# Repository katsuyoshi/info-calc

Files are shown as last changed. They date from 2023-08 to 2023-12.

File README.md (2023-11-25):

# 情報電卓 (Info Calc)

## 概要

電卓を様々な情報を表示する表示器にします。  
ESP NOWで外部からデータを受信することで温度や湿度など様々なデータを表示できます。  
[タイマー表示させるサンプル](platformio/timer_publisher)をM5StickCに書き込むみAボタンをおしてタイマーをスタートさせるとタイマー表示が確認できます。

protopediaに登録していますので、そちらもご覧ください。

[情報電卓](https://protopedia.net/prototype/4227)

## 材料

- 電卓 Canon WS-1200H (恐らく廃品)
- M5Atom Matrix x 1
- FS90 x 3

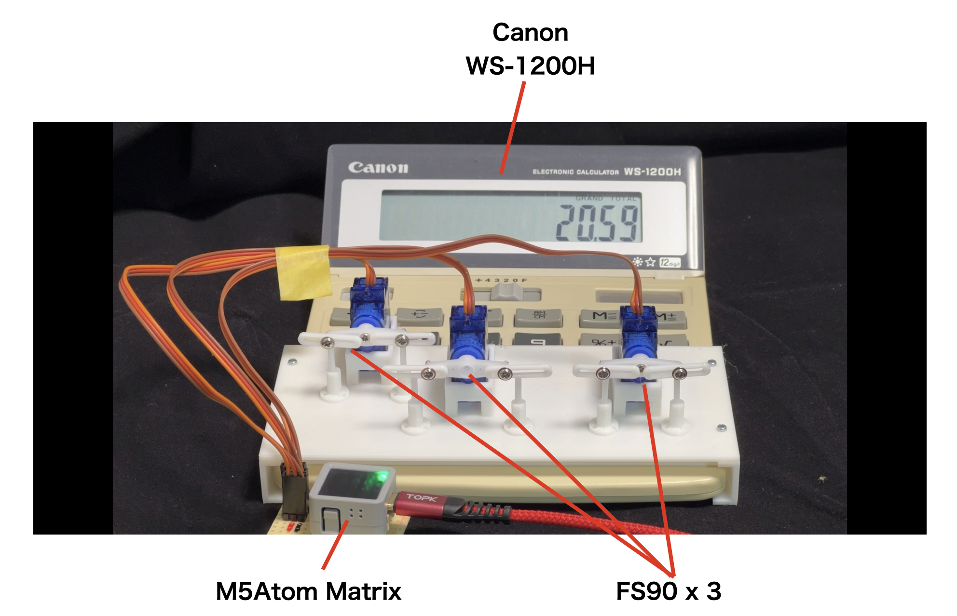
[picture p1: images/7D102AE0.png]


## 作り方

### 部品印刷

以下の2つの3Dモデルデータを3Dプリンターで印刷します。  
電卓によって変わるので設計し直しが必要と思われます。(データは参考程度です。)  

- [base_and_pushers.gcode](/3dmodels/base_and_pushers.gcode)
- [spacer.gcode](/3dmodels/spacer.gcode)

M2x6mmのネジでサイドの押さえと上面を止めます。  
サーボモーターもM2x6mmで止めます。  

棒状のサーボホーンとプッシャーをサーボモーター付属のネジで止めます。  

### 配線

以下の組みあせで配線します。

|M5Atom Matrix|FS90(=,+用)|FS90(.,0用)|FS90(1,CA用)|FS90(,-用)|備考|
|:--|:--|:--|:--|:--|:--|
|G22|橙||||100Ωの抵抗を間に入れてます|
|G19||橙|||100Ωの抵抗を間に入れてます|
|G23|||橙||100Ωの抵抗を間に入れてます|
|G33||||橙|100Ωの抵抗を間に入れてます|
|5V|赤|赤|赤|赤||
|GND|茶|茶|茶|茶||

### ソフトウェア書き込み

- このリポジトリをダウンロードします。
- VSCodeにPlatformIO拡張モジュールインストールし、[platformio/info_calc](/platformio/info_calc)フォルダを開きます。  
- 必要なライブラリーなど自動で読み込まれますので終わるまで待ちます。(下部ステータスバーでローディングのアニメーションが見えてる間)
- env.h.sampleをコピーしenv.hを作成します。
- 定数定義にSSIDとパスワードを書き込みます。
- USBケーブルでPCとM5Atom Matrixを繋ぎます。
- 下部ステータスバーの書き込みアイコン(レ点)を押して書き込みます。

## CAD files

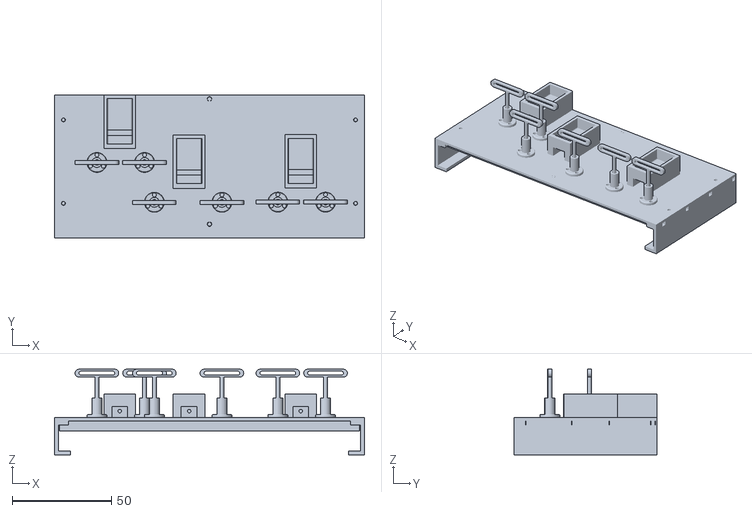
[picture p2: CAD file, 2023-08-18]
3dmodels/assembly.stl
156.0 x 72.1 x 43.1

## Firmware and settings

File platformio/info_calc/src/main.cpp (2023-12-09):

/*
MIT License

Copyright (c) 2023 Katsuyoshi Ito

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
THE SOFTWARE IS PROVIDED "AS IS", WITHOUT WARRANTY OF ANY KIND, EXPRESS OR
IMPLIED, INCLUDING BUT NOT LIMITED TO THE WARRANTIES OF MERCHANTABILITY,
FITNESS FOR A PARTICULAR PURPOSE AND NONINFRINGEMENT. IN NO EVENT SHALL THE
AUTHORS OR COPYRIGHT HOLDERS BE LIABLE FOR ANY CLAIM, DAMAGES OR OTHER
LIABILITY, WHETHER IN AN ACTION OF CONTRACT, TORT OR OTHERWISE, ARISING FROM,
OUT OF OR IN CONNECTION WITH THE SOFTWARE OR THE USE OR OTHER DEALINGS IN THE
SOFTWARE.
 */

#include <Arduino.h>
#include <M5Unified.h>
#include <ESP32Servo.h>
#include <WiFi.h>
#include <FastLED.h>
#include <time.h>
#include <esp_now.h>
#include "led.h"
#include "pusher.h"
#include "light.h"
#include "env.h"

// for LEDs
#define NUM_LEDS 25
#define LED_DATA_PIN 27
#define BRIGHTNESS  50

CRGB leds[NUM_LEDS];

// for ntp server

static const char *ntpServer = "ntp.nict.jp";
static const long gmtOffset_sec = 9 * 3600;
static const int daylightOffset_sec = 0;

static bool time_available = false;
static struct tm currentTime;


#define INVALID_DATA_INTERVAL   1 * 60 * 60 * 1000

// showing data rounding
#define ROUNDING_INTERVAL      30 * 1000

static bool rounding = false;
static unsigned long rounding_at = 0;

// Light pattern
enum LightPattern {
    LIGHT_OFF,
    LIGHT_NORMAL,
    LIGHT_JUST_HOUR,
    LIGHT_TIMER,
    LIGHT_LESS_ONE_MINITUE,
    LIGHT_LESS_THIRTY_SECONDS,
    LIGHT_LESS_TEN_SECONDS,
    LIGHT_LESS_FIVE_SECONDS,
    LIGHT_BANG,
    LIGHT_THREE_FEAVER,
    LIGHT_FOUR_FEVER,
};


struct ChannelValue {
    float value;
    unsigned long received_at;
    bool available;
    char unit[16];
};

static Pusher pushers[] = {
    Pusher(22, 11, 10, 9),      // A: =, B: +
    Pusher(19, 16, 17, 9),      // A: ., B: 0
    Pusher(23, 16, 16, 11),     // A: 1, B: CA
    Pusher(33, 10, 10, 8),      // A:  , B: -
};

static Light light = Light(32, 26, 25);

void move_servos()
{
    for (int i = 0; i < 3; i++)
    {
        pushers[i].move_next();
    }
}

// display time on a calculator.
class Calculator
{
    typedef enum
    {
        Unknown,
        Clear,

        Add1Minute,
        Add10Minutes,

        Add1Hour,
        Add10Hours,
        Add100Hours,

        Sub1Minute,
        Sub10Minutes,

        Sub1Hour,
        Sub10Hours,
        Sub100Hours,
    } mode;

    typedef enum
    {
        UnitUnknown,
        UnitClock,
        UnitTimer,
        UnitTemperature,
        UnitHumidity,
    } unit_type;

private:
    mode _mode = Unknown;
    int _value = 0;
    int _digit_values[4];
    char *_unit_pattern;
    unit_type _unit = UnitClock;
    LightPattern _light_pattern = LIGHT_NORMAL;

public:

    unit_type unit() { return _unit; }
    LightPattern light_pattern() { return _light_pattern; }
    void set_light_pattern(LightPattern pat) { _light_pattern = pat; }

    void set_time(int hour, int minute)
    {
        if (_mode == Unknown)
        {
            clear_all();
        }
        set_unit("clock");
        set_value((float)hour + (float)minute / 100.0);
    }

    void set_channel_value(ChannelValue *channel_value) {
        if (channel_value->available == false) { return; }

        set_unit(channel_value->unit);
        set_value(channel_value->value);
    }

    void clear_all()
    {
        push_clear_all();
        push_equal();
        _mode = Clear;
        _value = 0;
        for (int i = 0; i < 4; i++) {
            _digit_values[i] = 0;
        }
        _unit_pattern = NULL;
    }

    void set_unit(const char *unit) {
        const char *units[] = {
            "clock",
            "timer",
            "°C",
            "%"
        };

        int num = sizeof(units) / sizeof(units[0]);
        const char **ptr = &units[0];
        char *pattern = NULL;

        for (int i = 0; i < num; i++) {
            if (strcmp(*ptr++, unit) == 0) {
                switch (i) {
                    case 0:
                        pattern = led_clock_pattern;
                        _unit = UnitClock;
                        break;
                    case 1:
                        pattern = led_timer_pattern;
                        _unit = UnitTimer;
                        break;
                    case 2:
                        if (_value < 1000) {
                            pattern = led_cold_temperature;
                        } else
                        if (_value > 2500) {
                            pattern = led_hot_temperature;
                        } else {
                            pattern = led_norm_temperature;
                        }
                        _unit = UnitTemperature;
                        break;
                    case 3:
                        if (_value < 3333) {
                            pattern = led_low_humidity;
                        } else
                        if (_value > 6666) {
                            pattern = led_high_humidity;
                        } else {
                            pattern = led_norm_humidity;
                        }
                        _unit = UnitHumidity;
                        break;
                    default:
                        _unit = UnitUnknown;
                        break;
                }
            }
        }

        if (pattern == NULL) { return; }
        if (pattern == _unit_pattern) { return; }
        _unit_pattern = pattern;
        Serial.println(_unit_pattern);

        char *ch = _unit_pattern;
        // Reverse the order of the set values for an upside-down arrangement.
        for (int i = NUM_LEDS - 1; i >= 0; i--) {
            switch (*ch++) {
                case 'R':
                    leds[i] = CRGB::Red;
                    break;
                case 'G':
                    leds[i] = CRGB::Green;
                    break;
                case 'B':
                    leds[i] = CRGB::Blue;
                    break;
                default:
                    leds[i] = CRGB::Black;
                    break;
            }
        }
        FastLED.show();
    }

#if defined(TEST_MODE) || defined(TEST_COUNT_UP_DOWN)
public:
#else
private:
#endif

    void push_clear_all()
    {
        pushers[2].push_b();
        Serial.print("C");
    }

    void push_one()
    {
        pushers[2].push_a();
        Serial.print("1");
    }

    void push_zero()
    {
        pushers[1].push_b();
        Serial.print("0");
    }

    void push_dot()
    {
        pushers[1].push_a();
        Serial.print(".");
    }

    void push_plus()
    {
        pushers[0].push_b();
        Serial.print("+");
    }

    void push_equal()
    {
        pushers[0].push_a();
        Serial.print("=");
    }

    void push_minus()
    {
        pushers[3].push_b();
        Serial.print("-");
    }

private:

    void add_ten_minutes(int times)
    {
        if (times == 0)
        {
            return;
        }
        if (_mode != Add10Minutes)
        {
            push_plus();
            push_dot();
            push_one();
            _mode = Add10Minutes;
        }
        for (int i = 0; i < times; i++)
        {
            push_equal();
            _value += 10;
        }
    }

    void sub_ten_minutes(int times)
    {
        if (times == 0)
        {
            return;
        }
        if (_mode != Sub10Minutes)
        {
            push_minus();
            push_dot();
            push_one();
            _mode = Sub10Minutes;
        }
        for (int i = 0; i < times; i++)
        {
            push_equal();
            _value -= 10;
        }
    }

    void add_one_minute(int times)
    {
        if (times == 0)
        {
            return;
        }
        if (_mode != Add1Minute)
        {
            push_plus();
            push_dot();
            push_zero();
            push_one();
            _mode = Add1Minute;
        }
        for (int i = 0; i < times; i++)
        {
            push_equal();
            _value += 1;
        }
    }

    void sub_one_minute(int times)
    {
        if (times == 0)
        {
            return;
        }
        if (_mode != Sub1Minute)
        {
            push_minus();
            push_dot();
            push_zero();
            push_one();
            _mode = Sub1Minute;
        }
        for (int i = 0; i < times; i++)
        {
            push_equal();
            _value -= 1;
        }
    }

    void add_hundred_hours(int times)
    {
        if (times == 0)
        {
            return;
        }
        if (_mode != Add100Hours)
        {
            push_plus();
            push_one();
            push_zero();
            push_zero();
            _mode = Add100Hours;
        }
        for (int i = 0; i < times; i++)
        {
            push_equal();
            _value += 10000;
        }
    }

    void sub_hundred_hours(int times)
    {
        if (times == 0)
        {
            return;
        }
        if (_mode != Sub100Hours)
        {
            push_minus();
            push_one();
            push_zero();
            push_zero();
            _mode = Sub100Hours;
        }
        for (int i = 0; i < times; i++)
        {
            push_equal();
            _value -= 10000;
        }
    }

    void add_ten_hours(int times)
    {
        if (times == 0)
        {
            return;
        }
        if (_mode != Add10Hours)
        {
            push_plus();
            push_one();
            push_zero();
            _mode = Add10Hours;
        }
        for (int i = 0; i < times; i++)
        {
            push_equal();
            _value += 1000;
        }
    }

    void sub_ten_hours(int times)
    {
        if (times == 0)
        {
            return;
        }
        if (_mode != Sub10Hours)
        {
            push_minus();
            push_one();
            push_zero();
            _mode = Sub10Hours;
        }
        for (int i = 0; i < times; i++)
        {
            push_equal();
            _value -= 1000;
        }
    }

    void add_one_hour(int times)
    {
        if (times == 0)
        {
            return;
        }
        if (_mode != Add1Hour)
        {
            push_plus();
            push_one();
            _mode = Add1Hour;
        }
        for (int i = 0; i < times; i++)
        {
            push_equal();
            _value += 100;
        }
    }

    void sub_one_hour(int times)
    {
        if (times == 0)
        {
            return;
        }
        if (_mode != Sub1Hour)
        {
            push_minus();
            push_one();
            _mode = Sub1Hour;
        }
        for (int i = 0; i < times; i++)
        {
            push_equal();
            _value -= 100;
        }
   }

    void set_digit(int number, int digit) {
        if (number == 0) { return; }

        bool sign = number >= 0;
        number = abs(number);
        if (number > 5) {
            number = 10 - number;
            sign = !sign;
        }

        switch (digit) {
            case 0:
                {
                    if (sign) {
                        add_one_minute(number);
                    } else {
                        sub_one_minute(number);
                    }
                }
                break;
            case 1:
                {
                    if (sign) {
                        add_ten_minutes(number);
                    } else {
                        sub_ten_minutes(number);
                   }
                }
                break;

            case 2:
                {
                    if (sign) {
                        add_one_hour(number);
                    } else {
                        sub_one_hour(number);
                    }
                }
                break;
            case 3:
                {
                    if (sign) {
                        add_ten_hours(number);
                    } else {
                        sub_ten_hours(number);
                    }
                }
                break;
            case 4:
                {
                    if (sign) {
                        add_hundred_hours(number);
                    } else {
                        sub_hundred_hours(number);
                    }
                }
                break;
            defualt:
                return;
        }
    }

#if defined(TEST_MODE) || defined(TEST_COUNT_UP_DOWN)
public:
#endif

    void set_value(float value) {
        int v = (value * 100 + 0.5);
        if (_value == v) return;

Serial.printf("set_value %.2f -> \t", value);

        int base = 1;

        for (int digit = 0; digit < 5; digit++) {
            if (_value == v) break;
            int n = v - _value;
            n = (n / base) % 10;
            set_digit(n, digit);
            base *= 10;
        }
Serial.printf("\t-> _value %d, v: %d\n", _value, v);

Serial.printf("unit %d\n", _unit);
        switch(_unit) {
        case UnitTimer:
            if (_value >= 100) {
                _light_pattern = LIGHT_TIMER;
            } else
            if (_value >= 30) {
                _light_pattern = LIGHT_LESS_ONE_MINITUE;
            } else
            if (_value >= 10) {
                _light_pattern = LIGHT_LESS_THIRTY_SECONDS;
            } else
            if (_value >= 5) {
                _light_pattern = LIGHT_LESS_TEN_SECONDS;
            } else
            if (_value > 0) {
                _light_pattern = LIGHT_LESS_FIVE_SECONDS;
            } else {
                _light_pattern = LIGHT_FOUR_FEVER;
            }
            break;

        case UnitClock:
            if ((_value % 100 == 0) && (currentTime.tm_sec < 2)) {
                _light_pattern = LIGHT_JUST_HOUR;
                break;
            } else {
                _light_pattern = LIGHT_NORMAL;
                // 分が00でない場合はdefaultでも判断させるためbreakなし。
            }

        default:
            if ((_value < 1000) && (_value % 111 == 0)) {
                _light_pattern = LIGHT_THREE_FEAVER;
            } else
            if (_value % 1111 == 0) {
                _light_pattern = LIGHT_FOUR_FEVER;
            } else {
                _light_pattern = LIGHT_NORMAL;
            }
            break;
        }
    }
};

static Calculator calc = Calculator();

#define NUMBER_OF_CHANNEL       11

static int current_channel = 0;
static struct ChannelValue channel_values[NUMBER_OF_CHANNEL];
static unsigned long last_received_at = 0;

static esp_now_peer_info_t espnow_slave;
static bool espnow_setuped = false;

static void set_rounding(bool f, bool update = false) {
    if (update == false && rounding == f) { return; }
    
    rounding = f;
    if (update) {
        rounding_at = millis();
    } else {
        // for rounding immediately
        rounding_at = millis() - ROUNDING_INTERVAL;
    }
}

static void update_time()
{
    if (!getLocalTime(&currentTime))
    {
        Serial.println("Failed to obtain time");
        return;
    }
    time_available = true;
    Serial.println(&currentTime, "%Y %m %d %a %H:%M:%S");
}

static void espnow_on_data_receive(const uint8_t *mac_addr, const uint8_t *data, int data_len)
{
    ushort ch = 0;
    float value = 0.0f;
    char unit[16] = { 0 };
    char buff[64] = { 0 };
    ChannelValue *channel_value;

    strncpy(buff, (const char *)data, min(data_len, 63));
    
    sscanf(buff, "%hd,%f,%s\n", &ch, &value, unit);
    if (ch < 1 || ch >= NUMBER_OF_CHANNEL) {
        Serial.printf("The channell is %d. ", ch);
        Serial.println("The channel should 1 to 10.");
        return;
    }

    channel_value = &channel_values[ch];
    channel_value->available = true;
    channel_value->value = value;
    channel_value->received_at = millis();
    strncpy(channel_value->unit, unit, 15);

    Serial.printf("<< %s\n", buff);

    // タイマーの場合は継続して表示させるためラウンデングモードにせず直ぐにチャンネルを変更する。
    bool rounding = strcmp(unit, "timer") != 0;
    if (rounding == false) {
        current_channel = ch;
    }
    set_rounding(rounding);
    last_received_at = millis();
}

// @refer: https://it-evo.jp/blog/blog-1397/
static void espnow_setup_if_needed()
{
    if (espnow_setuped) return;

    WiFi.mode(WIFI_STA);
    WiFi.disconnect();
    if (esp_now_init() == ESP_OK)
    {
        Serial.println("ESPNow Init Success");
        espnow_setuped = true;
    }
    else
    {
        Serial.println("ESPNow Init Failed");
        espnow_setuped = false;
        ESP.restart();
        return;
    }

    memset(&espnow_slave, 0, sizeof(espnow_slave));
    for (int i = 0; i < 6; ++i)
    {
        espnow_slave.peer_addr[i] = (uint8_t)0xff;
    }

    esp_err_t addStatus = esp_now_add_peer(&espnow_slave);
    if (addStatus == ESP_OK)
    {
        Serial.println("Pair success");
    }
    esp_now_register_recv_cb(espnow_on_data_receive);
    last_received_at = millis();
}
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
void loop()
{
    static int n = 0;
    static int test_state = 0;
    M5.update();

#ifdef TEST_MODE
    test_mode();
    return;
#endif
#ifdef TEST_COUNT_UP_DOWN
    test_count_up_down();
    return;
#endif
#ifdef TEST_LIGHT_PATTERN
    test_light_patter();
    return;
#endif

    // Set it invalid after one hour past
    unsigned long now = millis();
    bool needs_to_change_current_channel = false;
    for (int i = 1; i < NUMBER_OF_CHANNEL; i++) {
        ChannelValue *channel_value = &channel_values[i];

        if (channel_value->available &&
            (now - channel_value->received_at >= INVALID_DATA_INTERVAL)) {
            channel_value->available = false;
            Serial.println("Invalid data");
            if (i == current_channel) {
                needs_to_change_current_channel = true;
            }
        }
    }

    // ラウンディングモード時はROUNDING_INTERVAL経過で次のチャンネルを表示する。
    if (rounding) {
        if (now - rounding_at >= ROUNDING_INTERVAL) {
            needs_to_change_current_channel = true;
            set_rounding(true, true);
        }
    } else {
        if (current_channel != 0) {
            // 最後の受信からROUNDING_INTERVAL経過したらラウンディングモードに戻す。
            if (now - last_received_at >= ROUNDING_INTERVAL) {
                // タイマーの場合は終了しているので無効にする。
                if (strcmp(channel_values[current_channel].unit, "timer") == 0) {
                    channel_values[current_channel].available = false;
                }
                needs_to_change_current_channel = true;
                set_rounding(true, true);
            }
        }
    }

    if (M5.BtnA.wasPressed() || needs_to_change_current_channel)
    {
        int ch = current_channel;
        for (int i = 0; i < NUMBER_OF_CHANNEL; i++) {
            ch = (ch + 1) % NUMBER_OF_CHANNEL;
            if (channel_values[ch].available) {
                break;
            }
        }
        if (current_channel == ch) { return; }

        current_channel = ch;
        Serial.printf("The current channel is %d\n", current_channel);
        // Quit the rounding mode if channel no is return to zero.
        if (current_channel == 0) {
            set_rounding(false);
        }
        display();
    }

    if (M5.BtnA.wasReleaseFor(1000)) {
        current_channel = 0;
        calc.clear_all();
        display();
    }

    // update time
    if (++n >= (1000 / 10))
    {
        n = 0;
        update_time();
        if (time_available) {
            espnow_setup_if_needed();
        }
    }

    display();
    delay(10);
}

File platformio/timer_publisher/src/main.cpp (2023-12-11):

#include <Arduino.h>
#include <M5Unified.h>
#include <WiFi.h>
#include <esp_now.h>
#include <EEPROM.h>

EEPROMClass  eeprom("eeprom");

esp_now_peer_info_t espnow_slave;

static bool started = false;
static unsigned long stopped_at = 0;
static int minitus = 1;
static int remains = minitus * 600;
static int preset = minitus * 600;

// @refer https://it-evo.jp/blog/blog-1397/
void espnow_on_data_sent(const uint8_t *mac_addr, esp_now_send_status_t status) {
  char macStr[18];
  snprintf(macStr, sizeof(macStr), "%02X:%02X:%02X:%02X:%02X:%02X",
           mac_addr[0], mac_addr[1], mac_addr[2], mac_addr[3], mac_addr[4], mac_addr[5]);
  //Serial.print("Last Packet Sent to: ");
  Serial.println(macStr);
  //Serial.print("Last Packet Send Status: ");
  Serial.println(status == ESP_NOW_SEND_SUCCESS ? "Delivery Success" : "Delivery Fail");
}


void espnow_setup() {
  WiFi.mode(WIFI_STA);
  WiFi.disconnect();
  if (esp_now_init() == ESP_OK) {
    Serial.println("ESPNow Init Success");
  } else {
    Serial.println("ESPNow Init Failed");
    ESP.restart();
  }

  memset(&espnow_slave, 0, sizeof(espnow_slave));
  for (int i = 0; i < 6; ++i) {
    espnow_slave.peer_addr[i] = (uint8_t)0xff;
  }
  
  esp_err_t addStatus = esp_now_add_peer(&espnow_slave);
  if (addStatus == ESP_OK) {
    Serial.println("Pair success");
  }

  esp_now_register_send_cb(espnow_on_data_sent);
}

void espnow_teardown()
{
  WiFi.disconnect();
  WiFi.mode(WIFI_OFF);
}

void espnow_send(int ch, float value, char *unit) {
  char str[64] = {};
  sprintf(str, "%i,%5.3f,%s", ch, value, unit);
Serial.println(str);
  esp_err_t result = esp_now_send(espnow_slave.peer_addr, (uint8_t *)str, strlen(str));
  Serial.print("Send Status: ");
  if (result == ESP_OK) {
    Serial.println("Success");
  } else if (result == ESP_ERR_ESPNOW_NOT_INIT) {
    Serial.println("ESPNOW not Init.");
  } else if (result == ESP_ERR_ESPNOW_ARG) {
    Serial.println("Invalid Argument");
  } else if (result == ESP_ERR_ESPNOW_INTERNAL) {
    Serial.println("Internal Error");
  } else if (result == ESP_ERR_ESPNOW_NO_MEM) {
    Serial.println("ESP_ERR_ESPNOW_NO_MEM");
  } else if (result == ESP_ERR_ESPNOW_NOT_FOUND) {
    Serial.println("Peer not found.");
  } else {
    Serial.println("Not sure what happened");
  }
}

void set_minitus(int m) {
  minitus = m;
  remains = minitus * 60 * 10;
  preset = remains;
}

void load_settings() {
    int m;
    eeprom.get(0, m);
    set_minitus(max(1, minitus));
}

void store_settings() {
    int m;
    eeprom.get(0, m);
    if (m != minitus) {
        eeprom.put(0, minitus);
        eeprom.commit();
    }
}


void display() {
  M5.Lcd.clear();
  M5.Lcd.setColor(started ? GREEN : RED);
  M5.Lcd.setCursor(8, 4);
  M5.Lcd.setTextSize(2);
  M5.Lcd.println(started ? "RUN" : "STOP");
  M5.Lcd.println();

  M5.Lcd.setTextSize(4);

  int m = remains / 600;
  int s = (remains / 10) % 60;
  M5.Lcd.printf(" %02d:%02d\n", m, s);
}

void setup() {
  auto cfg = M5.config();
  M5.begin(cfg);
  M5.Lcd.setRotation(1);
  M5.Lcd.setTextSize(3);

  eeprom.begin(4);
  load_settings();

  espnow_setup();
  display();

  stopped_at = millis();
}

void loop() {
  static unsigned long tick = millis();

  M5.update();

  if (M5.BtnA.wasPressed()) {
    Serial.println("Btn A was pressed");
    if (started == false && remains == 0) {
        set_minitus(minitus);
    } else {
      started = started ? false : true;
      if (started) {
        store_settings();
      }
    }
    display();
  }
  if (M5.BtnB.wasPressed()) {
    Serial.println("Btn B was pressed");
    if (started == false) {
      if (preset != remains) {
        set_minitus(minitus);
      } else {
        set_minitus(minitus + 1);
      }
    }
    display();
  }
  if (M5.BtnB.wasReleaseFor(1000)) {
    Serial.println("Btn B was long pressed");
    set_minitus(1);
    display();
  }

  unsigned long now = millis();
  if (now - tick >= 100) {
    tick = now;

    if (started) {
      if (remains % 10 == 0) {
        int v = remains / 10;
        int m = v / 60;
        int s = v % 60;
        float f = (float)m + (float)s * 0.01;
        espnow_send(3, f, "timer");
        display();
      }

      if (remains > 0) {
        remains--;
      } else {
        started = false;
        display();
      }
    }
  }

  // The device will automatically power off after two minutes when the timer stops.
  if (started) {
    stopped_at = millis();
  }
  if (millis() - stopped_at >= 2 * 60 * 1000) {
    M5.Power.powerOff();
  }

  delay(10);
}

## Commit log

2023-08-14 サーボモーター動作確認
2023-08-18 add a description to env.h.sample
2023-08-18 add 3d models
    [assembly.3mf]
2023-08-18 rename a folder
    [assembly.3mf, assembly.stl]
2023-09-10 add the rounding mode
    When it receives data, it turns to rounding mode.
    In rounding mode, it switches channels every thirty seconds, and then it back to channel zero, the rounding mode is finished.
2023-11-18 筐体とプッシャー変更後の再調整とサーボを一つ追加
2023-11-25 showable count down timer
2023-11-25 change location and add timer publisher sample
2023-11-27 時刻が更新されなくなるのを修正。
    CH0がavailableじゃなくなるせい？
2023-11-29 ライト点滅パターンの終了でLIGHT_NORMLに戻すやり方を修正。
    calc内で状態が管理されていて代入したlight_pattern変数を変えても状態を変えることができていなかった。
    calc内の状態を変更する様に修正。
2023-11-29 roundingモードoff時に動作させるつもりがifに他の条件も混ざっていて正しく処理されてなかったのを修正。
2023-11-29 clear_all()を削除する箇所の間違いを修正。
2023-12-09 improve timer publisher
    - Store preset to EEPROM
    - Improve the way to reset and increase the timer value.
    [main.cpp]
2023-12-11 Add auto power-off function
